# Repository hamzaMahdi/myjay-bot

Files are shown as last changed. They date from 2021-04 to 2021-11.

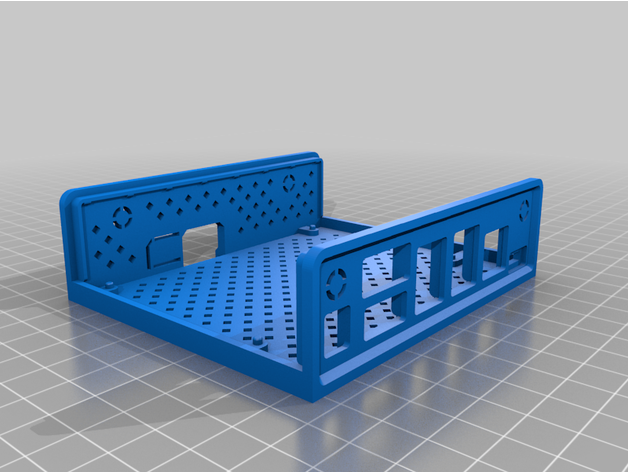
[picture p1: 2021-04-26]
3D/Solidworks/accessories/Nanobox/NanoBoxABS+for+B01/images/NanoBoxABSforB01_Bottom.png

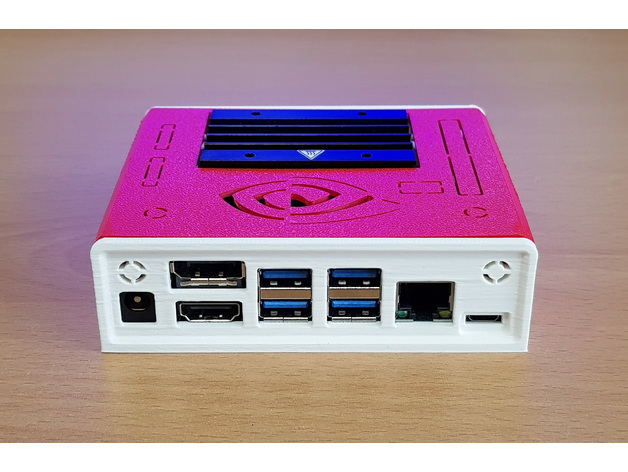
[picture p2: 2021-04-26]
3D/Solidworks/accessories/Nanobox/NanoBoxABS+for+B01/images/NanoBoxABSforB01_3.jpg

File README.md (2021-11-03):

# MyJay by SIRRL

This is the software/mechanical design repository for MyJay (formerly known as BeJay).

This is an ongoing project and is being updated irregularly. Code will be refactored and cleaned up eventually. For now, you can use my thesis (https://uwspace.uwaterloo.ca/handle/10012/17052) for technical details and for detailed Bill of Materials (BOM) if you'd like to build one yourself. If you end up using it, please cite it as:
```
@mastersthesis{mahdi2021developing,
  title={Developing a Semi-autonomous Robot to Engage Children with Special Needs and Their Peers in Robot-Assisted Play},
  author={Mahdi, Hamza},
  year={2021},
  school={University of Waterloo}
}
```

Full CAD of the robot can be found under the *3D* folder.

The robot currently uses a Jetson Nano to do vision tasks, localization, recieve teloperation commands over WIFI and control motors. The robot is ROS compatible and all packages can be found under the *catkin_ws* folder. Packages were developed for ROS Melodic, and may not be compatible with future versions especially because it uses Python 2.x 

Teleoperation scripts can run on any PC with WIFI. Scripts can be found in the *teleop_scripts* folder. Dependency documentation will be added.

*bejay_dev* is a folder for prototype scripts, which are later integrated into MyJay's ROS packages.

*test_scripts* houses random firmware written for the ESP32 with a prototype UDP protocol. This was for an earlier version of the robot which did not use the Jetson Nano compute module and ran exclusively on the ESP32 microcontroller.

**Remote Host Connection:**\
local ethernet: ssh bejay0@192.168.0.70\
local wifi: ssh bejay0@10.42.0.1

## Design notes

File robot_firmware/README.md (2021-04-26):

Use the bejay_rosserial project for typical operational firmware. The firmware should drive the LEDs and run the brushless flywheel motor.

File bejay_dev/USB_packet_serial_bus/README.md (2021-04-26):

This code is adapted from the repository that contains code to use the packet serial bus mode (multiple motor controllers) of the RoboClaw motor controller using the Basicmicro
Python library. The Application Note associated with this code can be [found here](https://resources.basicmicro.com/packet-serial-bus-operation-with-the-raspberry-pi-3/).

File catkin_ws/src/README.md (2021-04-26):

Packages in this folder are designed to run the basic functionalities of MyJay. 

MyJay is able to track balls based on color and uses a simple proportional controller to follow them. It can also stream its video feed over the network using the [`web_video_server`](http://wiki.ros.org/web_video_server) package. To start the tracker and the video streamer, simple run: `roslaunch myjay_cameras start_camera.launch`

The *robot_controller* package takes care of actuating and localizing the robot. By running `roslaunch myjay_core start_robot.launch`, the robot will listen to `/cmd_vel` messages for the drivetrain, `/intake` for the intake motor and `/elevator` for the upper elevator stage leading up to the flywheel. Additionally, the messages `/led` and `/flywheel` will be sent to the microcontroller via the `rosserial` node (please see `bejay_rosserial.ino` in the *robot_firmware* folder for more details).\
The *robot_controller* package is also responsible for localization using odometry. The robot needs a IMU for reliable localization (TODO).

The *myjay_teleop* package is responsible for receiving joystick teleoperation commands. It has two modes:
1. Local UDP mode: this recieves UDP messages from a local computer connected to the network. The scripts running on the local computer are `udp_adaptive.py` and `udp_joy_teleop.py` which can be found in the *teleop_scripts* folder.
2. Remote teleoperation over the internet using the firebase realtime database.

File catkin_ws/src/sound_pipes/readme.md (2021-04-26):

# sound_pipes

ROS package to play mp3 and wav files. 

*sound_pipes* create pipe for [mpg123](https://www.mpg123.de/) and [aplay](https://linux.die.net/man/1/aplay). 

This package is tested with ROS-Kinetic and Raspberry Pi 3B. 

## Install

```
cd ~/catkin_ws/src
git clone git@github.com:botamochi6277/sound_pipes.git
cd ~/catkin_ws/
catkin_make
```

## Sample Usage

Terminal1:

Execute a music player node. 

```
rosrun sound_pipes player
```

Terminal2:

Publish a full path of a music file, for exsample "/home/ubuntu/Music/music01.mp3"

```
rostopic pub -1 sound_pipes/sound std_msgs/String "<full path of sound>"
```

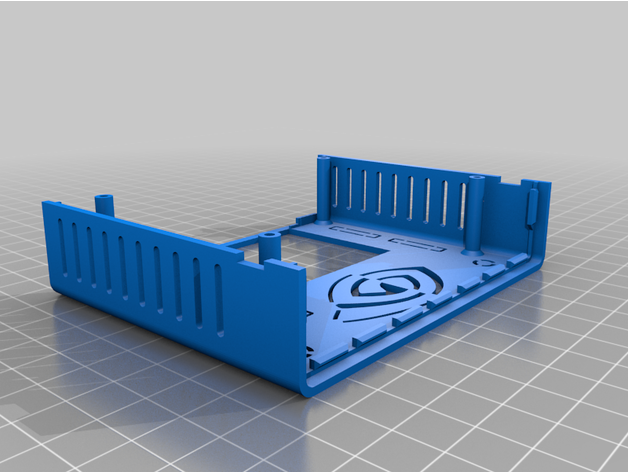
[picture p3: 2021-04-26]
3D/Solidworks/accessories/Nanobox/NanoBoxABS+for+B01/images/NanoBoxABSforB01_Top.png

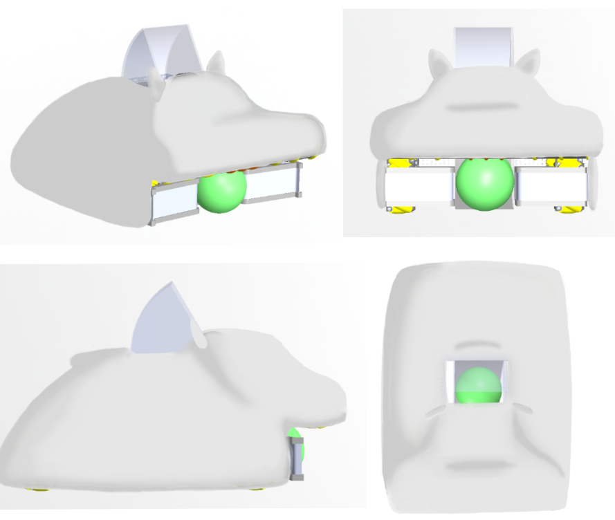
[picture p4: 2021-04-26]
3D/Sketches/cat.PNG

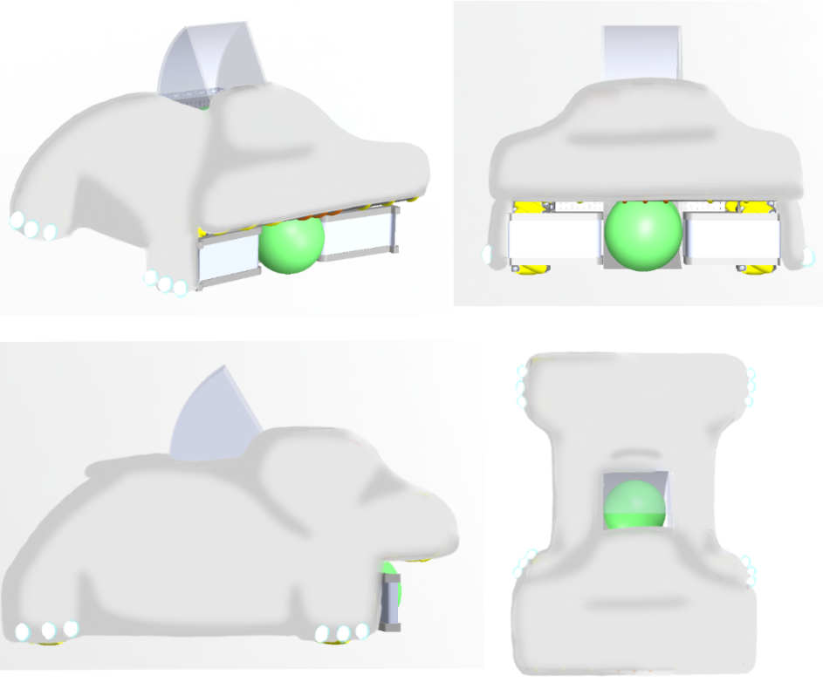
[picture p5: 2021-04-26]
3D/Sketches/toesl.PNG

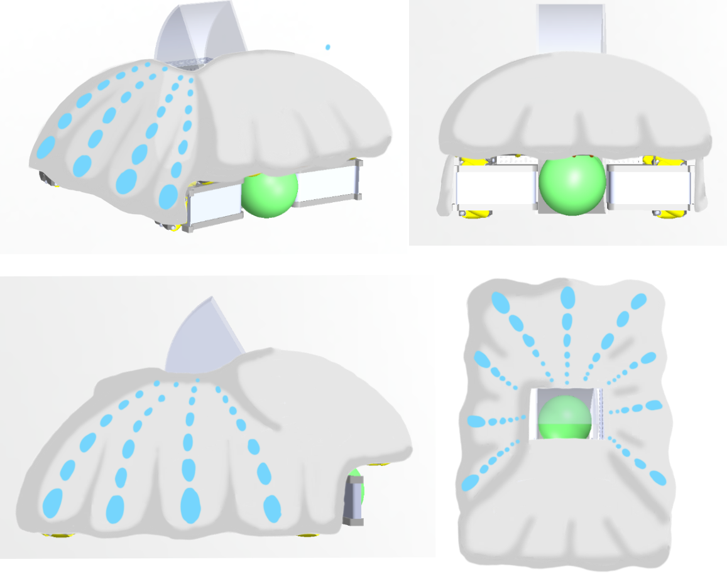
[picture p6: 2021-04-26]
3D/Sketches/cuttleab.PNG

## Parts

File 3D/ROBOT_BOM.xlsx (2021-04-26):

GOBILDA
Part | SKU | Amount | unit price (USD) | Price
Motion
Drivetrain kit | 3209-0001-0001 | 1 | 379.99 | 379.99
Mecanum wheel set | 3213-3606-0001 | 1 | 129.99 | 129.99
Intake+Elevator Motors | 5202-0002-0019 | 2 | 39.99 | 79.98
Backup motor (high rpm) | 5202-0002-0003 | 1 | 39.99 | 39.99
Bevel gear set | 3204-0002-0001 | 2 | 24.99 | 49.98
100 mm D shaft | 2101-0006-0100 | 6 | 2.39 | 14.34
144 mm, 12 mm diameter REX shaft | 2104-0012-0144 | 3 | 2.29 | 6.87
12 mm shaft collar | 2910-1026-4012 | 6 | 2.59 | 15.54
6 mm shaft collar (2 pack) | 2910-0816-0006 | 2 | 3.99 | 7.98
Hyperhub (6mm) | 1310-0016-1006 | 2 | 5.99 | 11.98
1611 Series Flanged Ball Bearing - 6mm ID x 14mm OD, 5mm Thickness | 1611-0514-0006 | 2 | 2.99 | 5.98
1611 Series Flanged Ball Bearing - 8mm ID x 14mm OD, 5mm Thickness | 1611-0514-0008 | 1 | 2.99 | 2.99
 |  |  |  | 0
Structure |  |  |  | 0
Low profile C-Channel | 1121-0015-0384 | 1 | 11.29 | 11.29
Side C-Channel (11 hole) | 1120-0011-0288 | 2 | 9.99 | 19.98
Side C-Channel (9 hole) | 1120-0009-0240 | 3 | 8.39 | 25.17
Quad block pattern mount | 1201-0043-0002 | 8 | 5.99 | 47.92
Side C-Channel (2 hole) | 1120-0002-0072 | 2 | 2.79 | 5.58
 |  |  |  | 0
 |  |  |  | 0
Electronics and Wiring |  |  |  | 0
Grommets | 2911-0014-0001 | 1 | 1.99 | 1.99
300 mm, 3.5 mm bullet connector wiring | 3800-0013-0300 | 6 | 1.99 | 11.94
Encoder breakout | 3801-0919-0300 | 2 | 3.99 | 7.98
 |  |  |  | 0
Standoffs |  |  |  | 0
18mm Standoff | 1501-0006-0180 | 1 | 1.89 | 1.89
24mm Standoff | 1501-0006-0240 | 1 | 2.19 | 2.19
46mm Standoff | 1501-0006-0460 | 1 | 3.29 | 3.29
16mm Standoff | 1501-0006-0160 | 1 | 1.79 | 1.79
 |  |  |  | 0
 |  |  |  | 0
AndyMark |  |  |  | 0
1/2 in. Hex ID Shielded Flanged Bearing | am-2986 | 2 | 6 | 12
3 in. Compliant Wheels | am-3946 | 1 | 7 | 7
1/2 in. Steel Hex Shaft Stock | am-0856 | 1 | 6 | 6
McmasterCarr |  |  |  | 0
Linear Motion Shaft (400 mm length, 8 mm diameter) | 6112K45 | 1 | 14.35 | 14.35
 |  |  | Total: | 925.97
While this is a comprehensive list, it's not final. This BOM is to be finalized

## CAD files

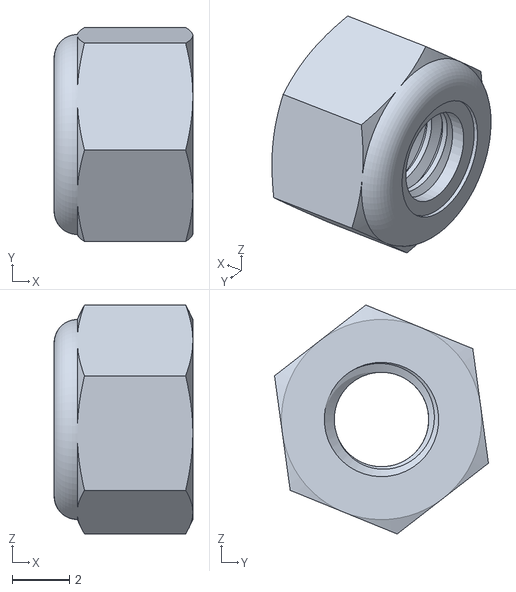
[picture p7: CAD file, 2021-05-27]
3D/Solidworks/Robot CAD FULL FINAL/Robot assembly - 3209-0001-0002_SUB_ASSEMBLY_1_ASM-1 gobilda mecanum wheel 1-1 2812-0004-0007_90576A103-2.STL
4.85 x 7.48 x 8.01

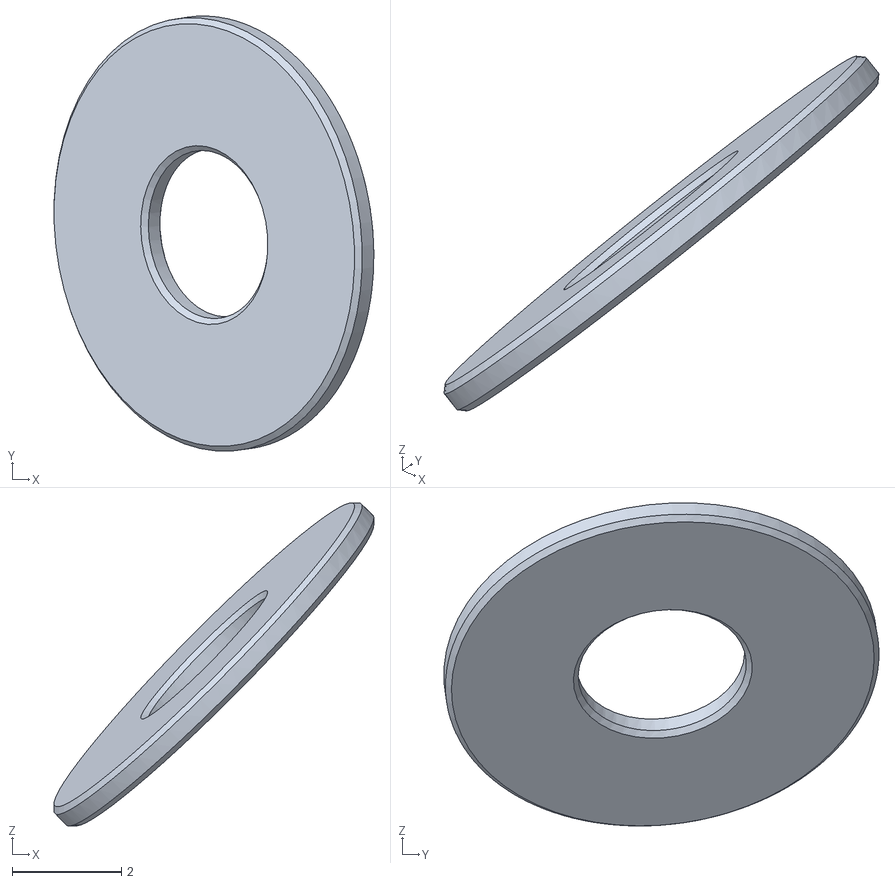
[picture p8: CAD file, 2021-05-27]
3D/Solidworks/Robot CAD FULL FINAL/Robot assembly - 3209-0001-0002_SUB_ASSEMBLY_1_ASM-1 gobilda mecanum wheel 1-1 3606-XXXX-0100 Roller Shim-13.STL
5.87 x 7.98 x 5.93

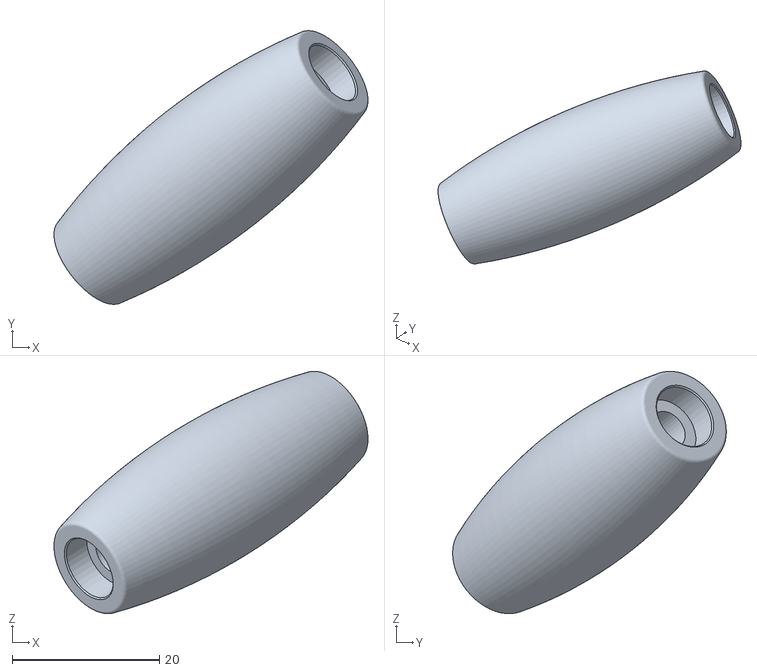
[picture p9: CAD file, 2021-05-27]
3D/Solidworks/Robot CAD FULL FINAL/Robot assembly - 3209-0001-0002_SUB_ASSEMBLY_1_ASM-1 gobilda mecanum wheel 1-2 3606-XXXX-0100 Hi Durability Roller-7.STL
42.7 x 37.2 x 32.9

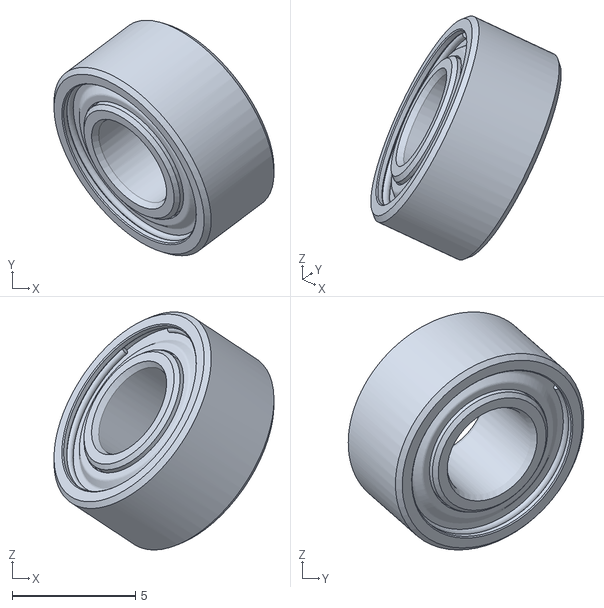
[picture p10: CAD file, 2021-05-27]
3D/Solidworks/Robot CAD FULL FINAL/Robot assembly - 3209-0001-0002_SUB_ASSEMBLY_1_ASM-1 gobilda mecanum wheel 1-2 3606-XXXX-0100 Roller Bearing-6.STL
8.91 x 9.54 x 9.64

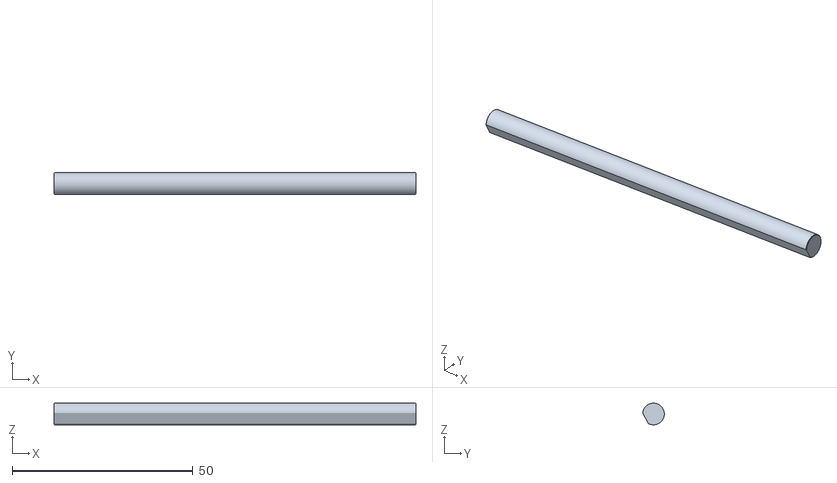
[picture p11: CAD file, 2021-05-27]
3D/Solidworks/Robot CAD FULL FINAL/Robot assembly - 3209-0001-0002_SUB_ASSEMBLY_1_ASM-1 2101-0006-0100-2.STL
100.0 x 5.99 x 6.00

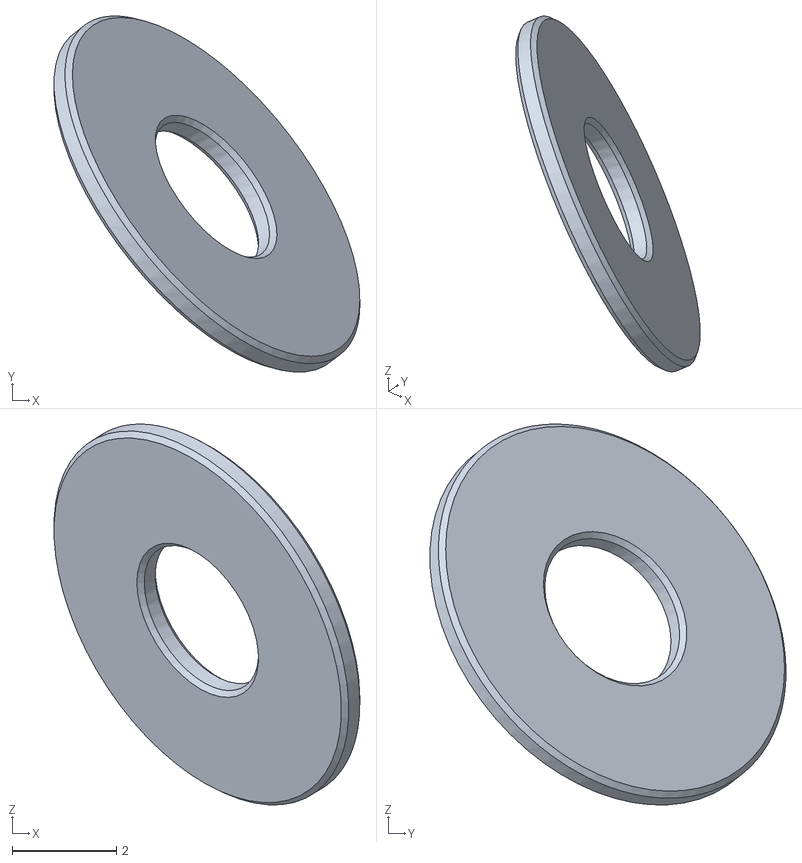
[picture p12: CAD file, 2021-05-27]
3D/Solidworks/Robot CAD FULL FINAL/Robot assembly - 3209-0001-0002_SUB_ASSEMBLY_1_ASM-1 gobilda mecanum wheel 1-1 3606-XXXX-0100 Roller Shim-16.STL
5.87 x 6.83 x 7.31

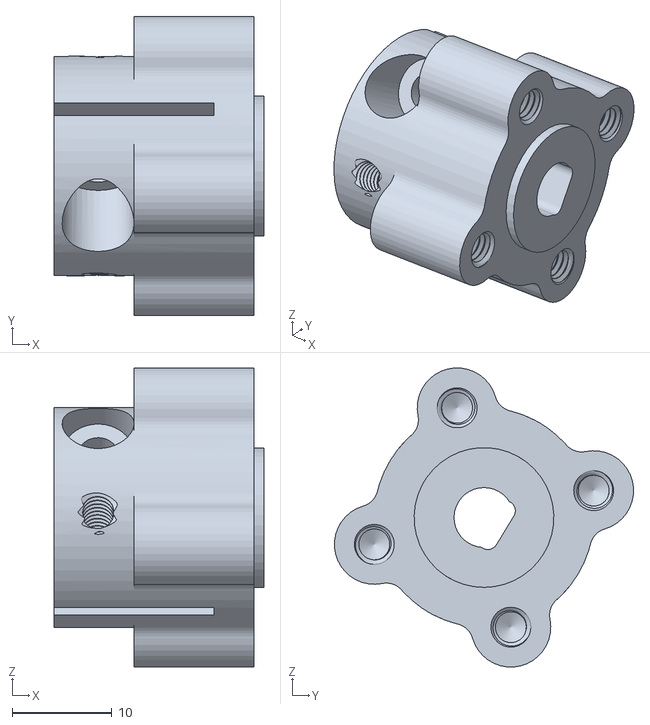
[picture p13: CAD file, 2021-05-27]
3D/Solidworks/Robot CAD FULL FINAL/Robot assembly - 3209-0001-0002_SUB_ASSEMBLY_1_ASM-1 1310-0016-1006_ASSEMBLY_ASM-2 1310-0016-1006-1.STL
21.0 x 30.0 x 30.0

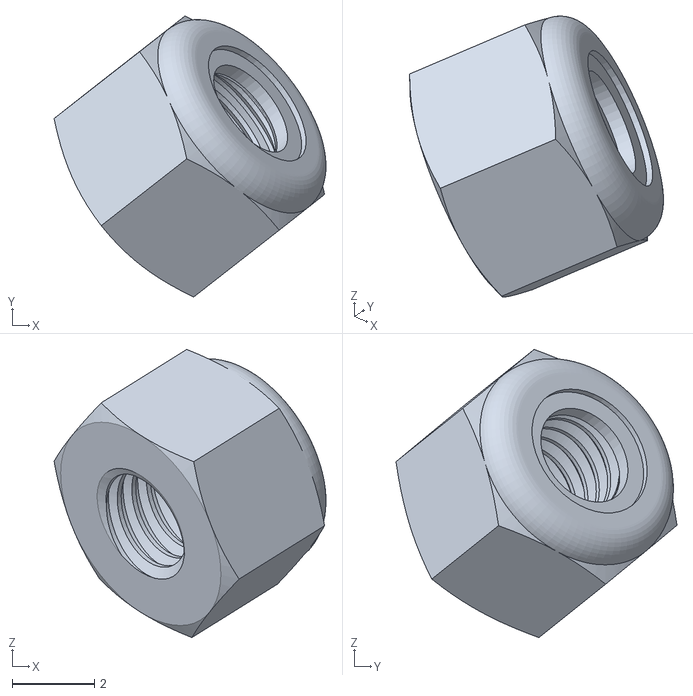
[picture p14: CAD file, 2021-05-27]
3D/Solidworks/Robot CAD FULL FINAL/Robot assembly - 3209-0001-0002_SUB_ASSEMBLY_1_ASM-1 gobilda mecanum wheel 1-2 3606-XXXX-0100 Roller Locknut_90576A102-16.STL
6.60 x 6.82 x 6.99

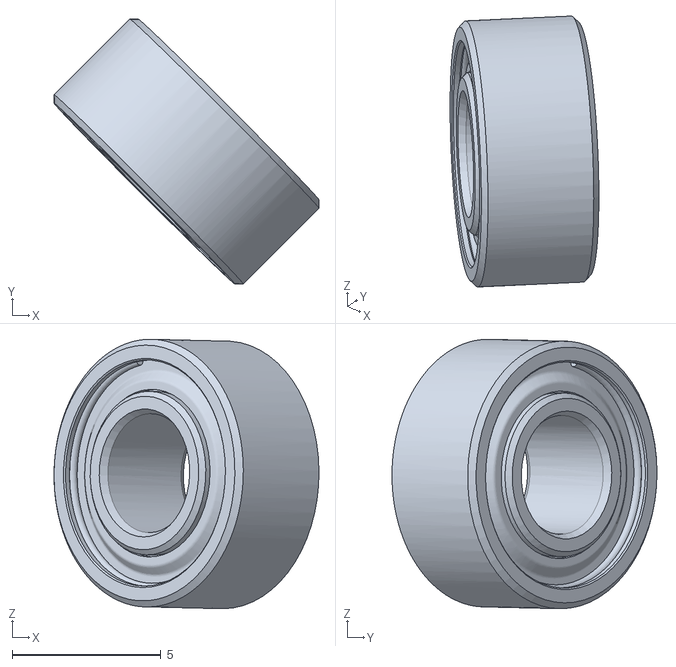
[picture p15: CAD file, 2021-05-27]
3D/Solidworks/Robot CAD FULL FINAL/Robot assembly - 3209-0001-0002_SUB_ASSEMBLY_1_ASM-1 gobilda mecanum wheel 1-2 3606-XXXX-0100 Roller Bearing-7.STL
8.91 x 8.91 x 9.06

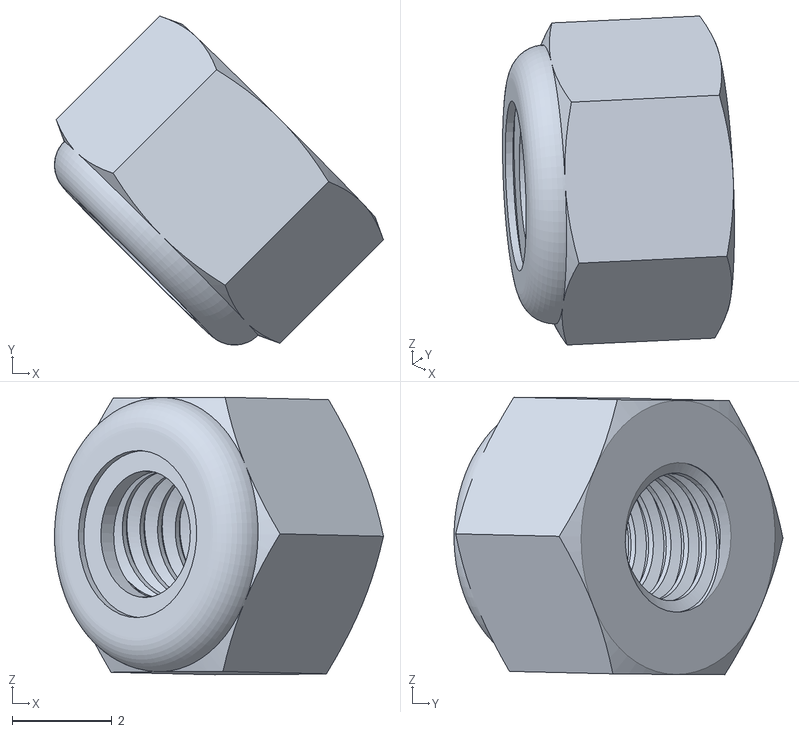
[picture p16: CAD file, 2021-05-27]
3D/Solidworks/Robot CAD FULL FINAL/Robot assembly - 3209-0001-0002_SUB_ASSEMBLY_1_ASM-1 gobilda mecanum wheel 1-2 3606-XXXX-0100 Roller Locknut_90576A102-7.STL
6.60 x 6.60 x 5.57

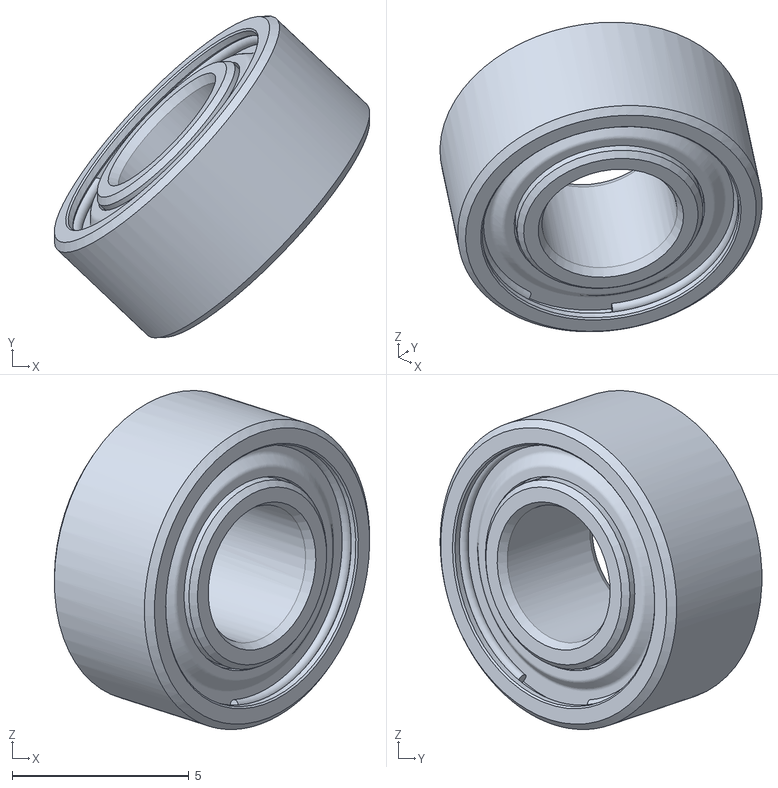
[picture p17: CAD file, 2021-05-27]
3D/Solidworks/Robot CAD FULL FINAL/Robot assembly - 3209-0001-0002_SUB_ASSEMBLY_1_ASM-1 gobilda mecanum wheel 1-2 3606-XXXX-0100 Roller Bearing-11.STL
8.91 x 9.09 x 9.58

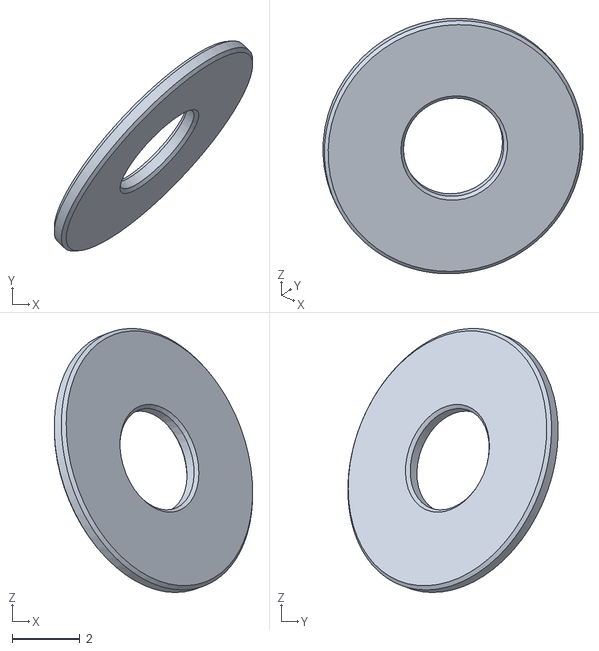
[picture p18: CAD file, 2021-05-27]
3D/Solidworks/Robot CAD FULL FINAL/Robot assembly - 3209-0001-0002_SUB_ASSEMBLY_1_ASM-1 gobilda mecanum wheel 1-2 3606-XXXX-0100 Roller Shim-1.STL
5.87 x 6.22 x 7.81

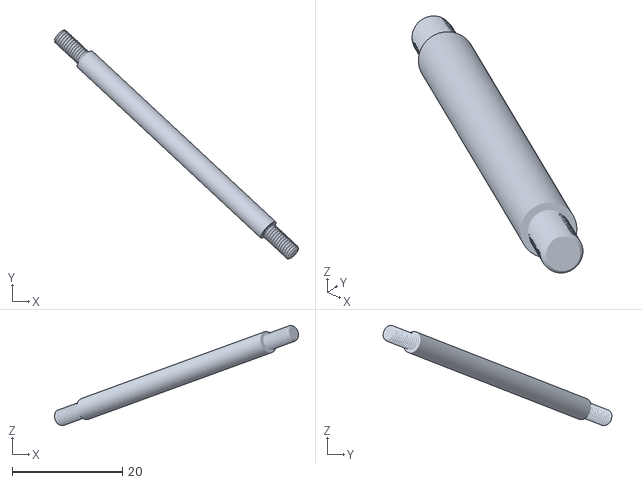
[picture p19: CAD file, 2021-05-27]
3D/Solidworks/Robot CAD FULL FINAL/Robot assembly - 3209-0001-0002_SUB_ASSEMBLY_1_ASM-1 gobilda mecanum wheel 1-2 3606-XXXX-0100 Roller Axle-1.STL
44.2 x 41.4 x 18.2

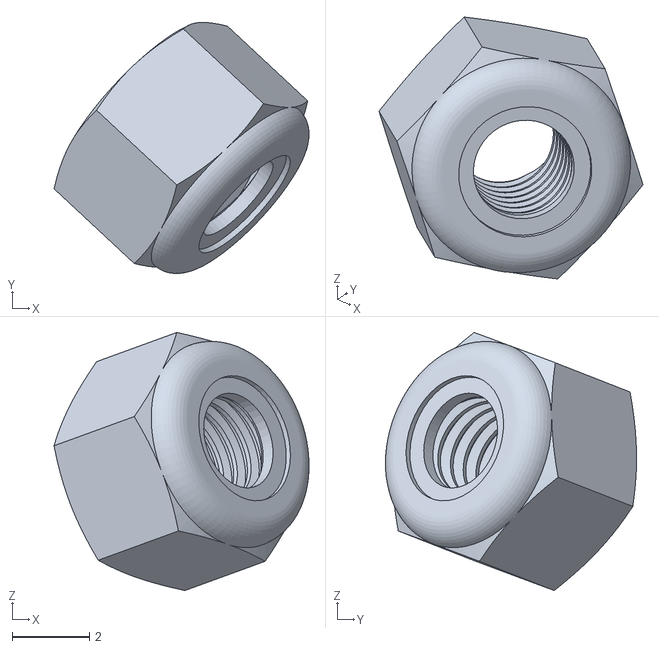
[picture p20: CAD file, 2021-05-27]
3D/Solidworks/Robot CAD FULL FINAL/Robot assembly - 3209-0001-0002_SUB_ASSEMBLY_1_ASM-1 gobilda mecanum wheel 1-2 3606-XXXX-0100 Roller Locknut_90576A102-1.STL
6.60 x 6.50 x 6.68

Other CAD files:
3D/Solidworks/Robot CAD FULL FINAL/1310-0016-1006_ASSEMBLY_ASM.sldasm
3D/Solidworks/Robot CAD FULL FINAL/3209-0001-0002_SUB_ASSEMBLY_4_1_ASM.sldasm
3D/Solidworks/Robot CAD FULL FINAL/Robot assembly - 3209-0001-0002_SUB_ASSEMBLY_1_ASM-1 gobilda mecanum wheel 1-2 3606-XXXX-0100 Roller Shim-8.STL
3D/Solidworks/Robot CAD FULL FINAL/Robot assembly - 3209-0001-0002_SUB_ASSEMBLY_1_ASM-1 gobilda mecanum wheel 1-2 3606-XXXX-0100 Roller Locknut_90576A102-8.STL
3D/Solidworks/Robot CAD FULL FINAL/1120-0007-0192.SLDPRT
3D/Solidworks/Robot CAD FULL FINAL/1120-0007-0192.STEP
3D/Solidworks/Robot CAD FULL FINAL/1120-0009-0240.sldprt
3D/Solidworks/Robot CAD FULL FINAL/1120-0011-0288.SLDPRT
3D/Solidworks/Robot CAD FULL FINAL/1120-0017-0432.sldprt
3D/Solidworks/Robot CAD FULL FINAL/1121-0011-0288.SLDPRT
3D/Solidworks/Robot CAD FULL FINAL/1121-0015-0384.SLDPRT
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

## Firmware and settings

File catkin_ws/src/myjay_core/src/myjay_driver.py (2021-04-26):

#!/usr/bin/env python
import rospy
import time 
from std_msgs.msg import Float32MultiArray
from std_msgs.msg import UInt8MultiArray
from std_msgs.msg import Float32
from std_msgs.msg import Int16
from std_msgs.msg import String
from geometry_msgs.msg import Quaternion, Twist
from sensor_msgs.msg import Imu
from nav_msgs.msg import Odometry
import tf
import serial
from myjay_core.roboclaw import Roboclaw
import numpy as np
import math
import subprocess
import os
stop  = False



# loosly based off mecanumbot and roboclaw_ros packages
class EncoderOdom:
    def __init__(self):

        rev_per_meter = 1/(math.pi*0.1)# 100 mm diameter wheel
        motor_rev_per_meter = rev_per_meter*2 #2:1 gear ratio
        ticks_per_meter = motor_rev_per_meter*383.6# 383.6 encoder counts per motor rev
        self.TICKS_PER_METER = ticks_per_meter
        self.BASE_WIDTH = 0.152*2 # 15.2 cm from wheel to center of robot
        # scales need calibration
        self.scale_x = 1
        self.scale_y = 1
        self.odom_pub = rospy.Publisher('/encoder_odom', Odometry, queue_size=10)
        self.actual_yaw_sub = rospy.Subscriber("/mpu_imu", Imu, self.get_actual_angle)
        self.cur_x = 0
        self.cur_y = 0
        self.cur_theta = 0.0
        self.actual_angle = 0.0
        self.last_enc_left1 = 0
        self.last_enc_left2 = 0
        self.last_enc_right1 = 0
        self.last_enc_right2 = 0
        self.last_enc_time = rospy.Time.now().secs

    @staticmethod
    def normalize_angle(angle):
        while angle > math.pi:
            angle -= 2.0 * math.pi
        while angle < -math.pi:
            angle += 2.0 * math.pi
        return angle

    # IMU subscriver callback
    def get_actual_angle(self, msg):
        orientation_q = msg.orientation
        orientation_list = [orientation_q.x, orientation_q.y, orientation_q.z, orientation_q.w]
        (roll, pitch, yaw) = tf.transformations.euler_from_quaternion(orientation_list)
        self.actual_angle = yaw

    def update(self, right_enc1, right_enc2, left_enc1, left_enc2):
        delta_left_ticks1 = left_enc1 - self.last_enc_left1
        delta_left_ticks2 = left_enc2 - self.last_enc_left2
        delta_right_ticks1 = right_enc1 - self.last_enc_right1
        delta_right_ticks2 = right_enc2 - self.last_enc_right2
        
        self.last_enc_left1 = left_enc1
        self.last_enc_left2 = left_enc2
        self.last_enc_right1 = right_enc1
        self.last_enc_right2 = right_enc2

        # convert the motor counts into x, y, theta counts
        dx = (delta_left_ticks1+ delta_right_ticks1 + delta_left_ticks1 + delta_right_ticks2) / 4.0
        dy = (0 -delta_left_ticks1+ delta_right_ticks1 + delta_left_ticks2 - delta_right_ticks2) / 4.0
        dx = dx*self.scale_x/self.TICKS_PER_METER
        dy = -dy*self.scale_y/self.TICKS_PER_METER
        
        # little fishy, will investigate later
        # https://github.com/joshvillbrandt/mecanumbot-ros-pkg/blob/master/arduino/libraries/Mecanum/Mecanum.cpp
        #dtheta = ( delta_left_ticks1- delta_right_ticks1 + delta_left_ticks1 - delta_right_ticks2) / 4.0
        #dtheta *=self.TICKS_PER_METER/self.BASE_WIDTH

        # more of a differential system. May not be correct
        dist_right = -(delta_right_ticks1+delta_right_ticks2)/ 2.0 / self.TICKS_PER_METER
        dist_left = (delta_left_ticks1+delta_left_ticks2) / 2.0/ self.TICKS_PER_METER
        dtheta = (dist_right - dist_left) / self.BASE_WIDTH

        dist = (dist_right + dist_left) / 4.0

        current_time = rospy.Time.now().secs
        d_time = (current_time - self.last_enc_time)
        self.last_enc_time = current_time


    
        self.cur_x += dx * math.cos(self.actual_angle)-dy*math.sin(self.actual_angle)
        self.cur_y += dx * math.sin(self.actual_angle)+dy*math.cos(self.actual_angle)
        self.cur_theta = self.normalize_angle(self.cur_theta + dtheta) # probably garbage value

        if abs(d_time) < 0.000001:
            vel_x = 0.0
            vel_y = 0.0
            vel_theta = 0.0
        else:
            vel_x = dx / d_time
            vel_y = dy/d_time
            vel_theta = dtheta / d_time

        return vel_x, vel_y, vel_theta

    def update_publish(self, right_enc1, right_enc2, left_enc1, left_enc2):
        # TODO: deal with encoder noise
        vel_x, vel_y, vel_theta = self.update(right_enc1, right_enc2, left_enc1, left_enc2)
        self.publish_odom(self.cur_x, self.cur_y, self.cur_theta, vel_x, vel_y, vel_theta)

    def publish_odom(self, cur_x, cur_y, cur_theta, vx, vy, vth):
        quat = tf.transformations.quaternion_from_euler(0, 0, self.actual_angle)
        current_time = rospy.Time.now()

        # replaced by robot_localization
        br = tf.TransformBroadcaster()
        br.sendTransform((cur_x, cur_y, 0),
                         tf.transformations.quaternion_from_euler(0, 0, self.actual_angle),
                         current_time,
                         "base_link",
                         "odom")

        odom = Odometry()
        odom.header.stamp = current_time
        odom.header.frame_id = 'odom'

        odom.pose.pose.position.x = cur_x
        odom.pose.pose.position.y = cur_y
        odom.pose.pose.position.z = 0.0
        odom.pose.pose.orientation = Quaternion(*quat)

        odom.pose.covariance[0] = 0.01
        odom.pose.covariance[7] = 0.01
        odom.pose.covariance[14] = 99999
        odom.pose.covariance[21] = 99999
        odom.pose.covariance[28] = 99999
        odom.pose.covariance[35] = 0.01

        odom.child_frame_id = 'base_link'
        odom.twist.twist.linear.x = vx
        odom.twist.twist.linear.y = vy
        odom.twist.twist.angular.z = vth
        odom.twist.covariance = odom.pose.covariance

        self.odom_pub.publish(odom)




class MyJay:
    def __init__(self):
        self.counter = 0
        self.init_robot()
        # self.odom_pub = rospy.Publisher("/odom", Int64, queue_size=10)# work in progress
        self.drive_train = rospy.Subscriber("/cmd_vel", Twist, self.callback_drive_robot)
        self.intake = rospy.Subscriber("/intake", Int16, self.callback_intake)
        self.elevator = rospy.Subscriber("/elevator", Int16, self.callback_elevator)

        # start with motors not moving
        self.intake_pwm = 64
        self.elevator_pwm = 64

        # health and heartbeat checks
        self.last_cmd_time = rospy.get_rostime().secs
        self.battery_pub = rospy.Publisher("/battery_voltage", Float32, queue_size =1)
        self.led_pub = rospy.Publisher("/led", UInt8MultiArray, queue_size =1)


        self.encoder_odom = EncoderOdom()


        #self.led_sub = rospy.Subscriber("/led", String, self.callback_set_led)

    # initiate roboclaws automatically. Needs prior knowledge of each address 
    def init_robot(self):
        # the arduino will ALWAYS be ttyUSB0 unless unplugged during operation
        # self.ser = serial.Serial('/dev/ttyUSB0',9600)

        # this depends on the physical connections in your robot
        self.right_address = 0x80
        self.left_address = 0x82
        self.intake_address = 0x81
        addresses = [self.right_address,self.left_address,self.intake_address]
        # it's better to create a udev rule with specific names but they all have the same attributes
        self.roboclaw = []
        self.roboclaw.append(Roboclaw("/dev/ttyACM0", 38400))
        self.roboclaw.append(Roboclaw("/dev/ttyACM1", 38400))
        self.roboclaw.append(Roboclaw("/dev/ttyACM2", 38400))


        print('setting up connections...')
        for rc_ind, rc in enumerate(self.roboclaw):
            rc.Open()
            for add_ind, address in enumerate(addresses):
                if(rc.ReadNVM(address) and address==self.right_address):
                    self.right_ind = rc_ind
                    break
                if(rc.ReadNVM(address) and address==self.intake_address):
                    self.intake_ind = rc_ind
                    break
                if(rc.ReadNVM(address) and address==self.left_address):
                    self.left_ind = rc_ind
                    break
        print('setup complete !')
        print('Battery Voltage Level:')
        self.battery_voltage = self.roboclaw[self.right_ind].ReadMainBatteryVoltage(self.right_address)[1]/10.0
        print(self.battery_voltage)

        # reset encoders
        self.stop_drive()
        self.roboclaw[self.right_ind].ResetEncoders(self.right_address)
        self.roboclaw[self.left_ind].ResetEncoders(self.left_address)
        self.drive_motor_pwm = [64,64,64,64] # stop
    

    # drive motors PWM
    def drive_pwm(self, l1, l2, r1, r2):
        self.roboclaw[self.left_ind].ForwardBackwardM1(self.left_address, l1)
        self.roboclaw[self.left_ind].ForwardBackwardM2(self.left_address, l2)
        self.roboclaw[self.right_ind].ForwardBackwardM2(self.right_address, r1)
        self.roboclaw[self.right_ind].ForwardBackwardM1(self.right_address, r2)

    # intake motor PWM
    def run_intake(self, Mspeed):
        self.roboclaw[self.intake_ind].ForwardBackwardM1(self.intake_address, Mspeed)

    # elevator motor PWM
    def run_elevator(self, Mspeed):
        self.roboclaw[self.intake_ind].ForwardBackwardM2(self.intake_address, Mspeed)

    # Stop all drive motors (usually in timeouts)
    def stop_drive(self):
        self.roboclaw[self.left_ind].ForwardM1(self.left_address, 0)
        self.roboclaw[self.left_ind].ForwardM2(self.left_address, 0)
        self.roboclaw[self.right_ind].ForwardM1(self.right_address, 0)
        self.roboclaw[self.right_ind].ForwardM2(self.right_address, 0)

    # needs PID tuning but the firmware is messed up for now
    def drive_vel(self, l1, l2, r1, r2):
        print("l1: ",l1,", l2: ",l2,", r1: ",r1,", r2: ",r2)
        self.roboclaw[self.left_ind].SpeedM1M2(self.left_address, l1, l2)
        self.roboclaw[self.right_ind].SpeedM1M2(self.right_address, r1, r2)

    # receive drivetrain commands in m/s
    def callback_drive_robot(self, msg):
        self.last_cmd_time = rospy.get_rostime()
        # kinematics formula can be found in the modern robotics textbook 
        # http://hades.mech.northwestern.edu/index.php/Modern_Robotics
        # all units are in meters
        l = 0.168 #distance between center of drivetrain and center of one of the wheels 
        w = 0.152 # distance half the distance between two opposite wheels ex(rear left and rear right)
        wheel_radius = 0.05 
        max_rps = 435.0/2/60
        max_ticks = max_rps*383.6 # quadrature enc/s
        max_omega = 435.0/2*2*math.pi/60 # 435 rpm motor with 2:1 gear ratio and convert to rad/s
        max_linear = max_omega*wheel_radius
        H = np.array([[-l-w,1,-1],[l+w,1,1],[l+w,1,-1],[-l-w,1,1]])
        V = np.array([[msg.angular.z],[msg.linear.x],[msg.linear.y]])
        u = 1/wheel_radius*H.dot(V)
        u_inverted = np.ravel(np.multiply(u.T,np.array([1,1,-1,-1]))) # invert motors (due to orientation)
        
        # scale and prepare for PWM (include feedback later)
        # the scale is VERY wrong but i put it here temporarily
        # u_inverted = np.interp(u_inverted, (-max_omega, max_omega), (0, 128)).astype(int)
        # u1, u2, u3, u4
        # front left, front right, back right, back left
        # print(u_inverted)
        
        self.drive_motor_pwm = np.interp(u_inverted, (-max_omega, max_omega), (0, 128)).astype(int)


        

        #u_inverted = np.interp(u_inverted, (-max_omega, max_omega), (-max_ticks, max_ticks)).astype(int)
        #self.drive_vel(u_inverted[0], u_inverted[3], u_inverted[1], u_inverted[2])

    # updsate intake pwm
    def callback_intake(self, run):
        self.intake_pwm = run.data

    # update elevator pwm
    def callback_elevator(self, run):
        self.elevator_pwm = run.data
    
    # update battery voltage and encoders
    def update_sensor_data(self):
        # any of the roboclaws work
        self.battery_voltage = self.roboclaw[self.right_ind].ReadMainBatteryVoltage(self.right_address)[1]/10.0

        # if the battery is too low show red on LED strip
        if self.battery_voltage<10:
            array = [0,100,0,0,100]
            self.led_pub.publish(UInt8MultiArray(data=array))
        
        self.battery_pub.publish(self.battery_voltage)


        # Read encoder
        # note:
        # Each motor rev is 383.6 ticks, 2:1 gear ratio-> 767.2 ticks
        try:
            status_l1, self.left_enc1, crcl1 = self.roboclaw[self.left_ind].ReadEncM1(self.left_address)
            status_l2, self.left_enc2, crcl2 = self.roboclaw[self.left_ind].ReadEncM2(self.left_address)
        except ValueError:
            pass
        except OSError as e:
            rospy.logwarn("ReadEnc Left OSError: %d", e.errno)
            rospy.loginfo(e)

        try:
            status_r1, self.right_enc1, crcr1 = self.roboclaw[self.right_ind].ReadEncM1(self.right_address)
            status_r2, self.right_enc2, crcr2 = self.roboclaw[self.right_ind].ReadEncM2(self.right_address)
        except ValueError:
            pass
        except OSError as e:
            rospy.logwarn("ReadEnc Right OSError: %d", e.errno)
            rospy.loginfo(e)
        
        self.encoder_odom.update_publish(self.right_enc1, self.right_enc2, -self.left_enc1, -self.left_enc2)
    

    def print_encoder_data(self):
        print("Left encder M1: %f",self.left_enc1)
        print("Left encder M2: %f",self.left_enc2)
        print("Right encder M1: %f",self.right_enc1)
        print("Right encder M2: %f",self.right_enc2)
        print("------------------------------")

if __name__ == '__main__':
    rospy.init_node('robot_controller')

    robot = MyJay()
    #rospy.spin()
    last_encoder_time = rospy.Time.now().secs # to be used to limit odometry calc rate
    odom_rate = 20.0 #20 hz
    

    rate = rospy.Rate(20) # ROS Rate at 20Hz
    while not rospy.is_shutdown():
        # intake and elevator are supposed to act instantaneously at a single speed
        robot.run_elevator(robot.elevator_pwm)
        robot.run_intake(robot.intake_pwm)


        # run drivetrain at the main loop's rate
        try:
            robot.drive_pwm(robot.drive_motor_pwm[0], robot.drive_motor_pwm[3],
             robot.drive_motor_pwm[1], robot.drive_motor_pwm[2])# front left, front right, back right, back left
        except OSError as e:
            rospy.loginfo("Motor OSError: %d", e.errno)
            rospy.loginfo(e)
        
        # update sensor data
        robot.update_sensor_data()

        rate.sleep()


        # sort of a watchdog
        # if (rospy.get_rostime() - robot.last_cmd_time).to_sec() > 1:
        #     # stop all drive motors so the robot doesnt break stuff (or itself)
        #     robot.stop_drive()

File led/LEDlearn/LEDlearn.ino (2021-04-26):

#include <Adafruit_NeoPixel.h>
#include <FastLED.h>

#define NUM_LEDS 50
#define PIN 23
Adafruit_NeoPixel strip = Adafruit_NeoPixel(NUM_LEDS, PIN, NEO_GRB + NEO_KHZ800);

CRGB leds[NUM_LEDS];


void setAll(byte red, byte green, byte blue) {
  for(int i = 0; i < NUM_LEDS; i++ ) {
    setPixel(i, red, green, blue);
  }
  showStrip();
}

void rainbowCycle(int SpeedDelay) {
  byte *c;
  uint16_t i, j;

  for(j=0; j<256*5; j++) { // 5 cycles of all colors on wheel
    for(i=0; i< NUM_LEDS; i++) {
      c=Wheel(((i * 256 / NUM_LEDS) + j) & 255);
      setPixel(i, *c, *(c+1), *(c+2));
    }
    showStrip();
    delay(SpeedDelay);
  }
}

byte * Wheel(byte WheelPos) {
  static byte c[3];
 
  if(WheelPos < 85) {
   c[0]=WheelPos * 3;
   c[1]=255 - WheelPos * 3;
   c[2]=0;
  } else if(WheelPos < 170) {
   WheelPos -= 85;
   c[0]=255 - WheelPos * 3;
   c[1]=0;
   c[2]=WheelPos * 3;
  } else {
   WheelPos -= 170;
   c[0]=0;
   c[1]=WheelPos * 3;
   c[2]=255 - WheelPos * 3;
  }

  return c;
}

void showStrip() {
 #ifdef ADAFRUIT_NEOPIXEL_H
   //NeoPixel
   strip.show();
 #endif
 #ifndef ADAFRUIT_NEOPIXEL_H
   //FastLED
   FastLED.show();
 #endif
}

void setPixel(int Pixel, byte red, byte green, byte blue) {
 #ifdef ADAFRUIT_NEOPIXEL_H
   // NeoPixel
   strip.setPixelColor(Pixel, strip.Color(red, green, blue));
 #endif
 #ifndef ADAFRUIT_NEOPIXEL_H
   // FastLED
   leds[Pixel].r = red;
   leds[Pixel].g = green;
   leds[Pixel].b = blue;
 #endif
}




void startup(){
    for(int k = 0; k < 256; k++) {
      
      setAll(0,0,k); 
      showStrip();
      delay(40);
    }
}

void oneColour(int red, int green, int blue)
{
  setAll(red, green, blue);
}



void RunningLightsForward(byte red, byte green, byte blue, int WaveDelay) {
  int Position=0;
 
  for(int j=0; j<NUM_LEDS*2; j++)
  {
      Position++; // = 0; //Position + Rate;
      for(int i=0; i<NUM_LEDS; i++) {
        // sine wave, 3 offset waves make a rainbow!
        //float level = sin(i+Position) * 127 + 128;
        //setPixel(i,level,0,0);
        //float level = sin(i+Position) * 127 + 128;
        setPixel(i,((sin(i+Position) * 127 + 128)/255)*red,
                   ((sin(i+Position) * 127 + 128)/255)*green,
                   ((sin(i+Position) * 127 + 128)/255)*blue);
      }
     
      showStrip();
      delay(WaveDelay);
  }
}


void RunningLightsBackward(byte red, byte green, byte blue, int WaveDelay) {
  int Position=0;
 
  for(int j=NUM_LEDS*2; j>0; j--)
  {
      Position--; // = 0; //Position + Rate;
      for(int i=0; i<NUM_LEDS; i++) {
        // sine wave, 3 offset waves make a rainbow!
        //float level = sin(i+Position) * 127 + 128;
        //setPixel(i,level,0,0);
        //float level = sin(i+Position) * 127 + 128;
        setPixel(i,((sin(i+Position) * 127 + 128)/255)*red,
                   ((sin(i+Position) * 127 + 128)/255)*green,
                   ((sin(i+Position) * 127 + 128)/255)*blue);
      }
     
      showStrip();
      delay(WaveDelay);
  }
}

void setup() { 
  strip.begin();
  strip.show(); 
  FastLED.addLeds<WS2812B, PIN, GRB>(leds, NUM_LEDS).setCorrection( TypicalLEDStrip );
}

void loop() {
  startup();
  rainbowCycle(3);
  RunningLightsForward(0xff,0xff,0x00, 50);
  RunningLightsBackward(0xff,0xff,0x00, 50);
  oneColour(255,0,0);
} 

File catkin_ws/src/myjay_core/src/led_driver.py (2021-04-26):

#!/usr/bin/env python

import time
import rospy
from std_msgs.msg import UInt8MultiArray
from std_msgs.msg import Int16
from geometry_msgs.msg import Twist


def callback_drive(msg):

    #ex: 
    # array = [0,10,0,10,10]
    # my_array_for_publishing = UInt8MultiArray(data=array)

    x = msg.linear.x
    y = msg.linear.y
    z = msg.angular.z
    #color states based on direction
    #    3: forward, 4: backward, 0: set all 
    #    5: right, 6: left
    #    7: rainbow
    #    second return is for color
    #    this seems inefficient fix later
    if x!=0 and abs(x)>abs(y):
        if x>0:
            array = [4,0,100,0,100]
            led_pub.publish(UInt8MultiArray(data=array))
        else:
            array = [3,100,0,0,100]
            led_pub.publish(UInt8MultiArray(data=array))
    elif y!=0:
        if y>0:
            array = [5,100,0,100,100]
            led_pub.publish(UInt8MultiArray(data=array))
        else:
            array = [6,0,0,100,100]
            led_pub.publish(UInt8MultiArray(data=array))
    else:
        array = [0,0,0,0,100]
        led_pub.publish(UInt8MultiArray(data=array))



# init the ros node and publishers
rospy.init_node('light_feedback')
led_pub = rospy.Publisher("/led", UInt8MultiArray, queue_size =1)
drive_train = rospy.Subscriber("/cmd_vel", Twist, callback_drive)




rospy.spin()

# while not rospy.is_shutdown():
#     flywheel_pub.publish(Int16(data=1500))
#     led_pub.publish(my_array_for_publishing)
#     time.sleep(0.1)

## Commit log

2021-04-26 commit before thesis
    [Camera Mount Ver 6 - Sept 10th.STL, HEAD - End - 12.STL, HEAD - Mid - 13.STL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]
2021-05-27 push final cad with shell finalized
    [1120-0007-0192.SLDPRT, 1120-0007-0192.STEP, 1120-0009-0240.sldprt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]
